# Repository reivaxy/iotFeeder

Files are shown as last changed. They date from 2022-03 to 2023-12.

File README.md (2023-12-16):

# iotFeeder

Page in french or other languages: https://github-com.translate.goog/reivaxy/iotFeeder?_x_tr_sl=en&_x_tr_tl=fr&_x_tr_hl=fr

## WiFi enabled fish feeder for aquarium. Notifies when empty, power off, ...

Main components: ESP8266, Oled screen, stepper motor, 3D printed Archimedes screw and case.

All settings are done using embedded web page forms over Wifi. It records activiyy in a Firebase DB (Google Cloud), and you will receive notifications when it's empty or offline.

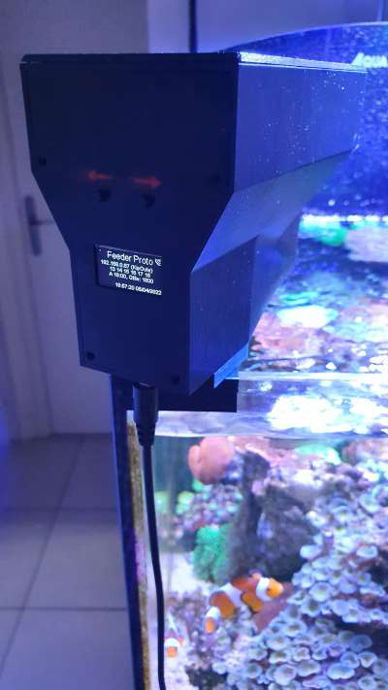
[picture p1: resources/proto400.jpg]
proto

```
DISCLAIMER of liability: this is a (fish) life sustaining device, all files are provided with no warranty of any kind. 

Building this device using these files and instructions means you implicitely accept to use it at your own risk, with proper supervision and monitoring to ensure your fishes are indeed fed as they should.

I can't be held responsible for any damage occurring while using a device you built using these files and instructions, whatever the reason (design flaw, software bug, ...)

If you do not agree with this disclaimer, do not build this device, or do not use it.
```

I've built 7 feeders with food IR detection (and one without), and a friend has built one.

4 are currently installed on small to big recifal fish tanks (salted water, tropical fishes and corals), and three on freshwater tank, running with no issue since begining of May 2022 for 2 of them, and since mid July 2022 for the others.

It will eventually be a module of the Iotinator framework (https://github.com/reivaxy/iotinator), but it can already work autonomously (no master module is needed).

It connects to your home Wifi network to fetch date/time and posts logs and alerts to Firebase (Google Cloud free account) as well as send push notifications when it detects that it's empty. Firebase will also send you push notifications when the module seems to be disconnected (power outage, wifi outage...)

It keeps working even if wifi goes out, but you'll get disconnection notifications, thanks to a google cloud function checking for ping records every 5mn.

Notifications are sent using Pushover.net, using a one-time-fee plan (about $5).

Logs and alerts are available on a google cloud application page:

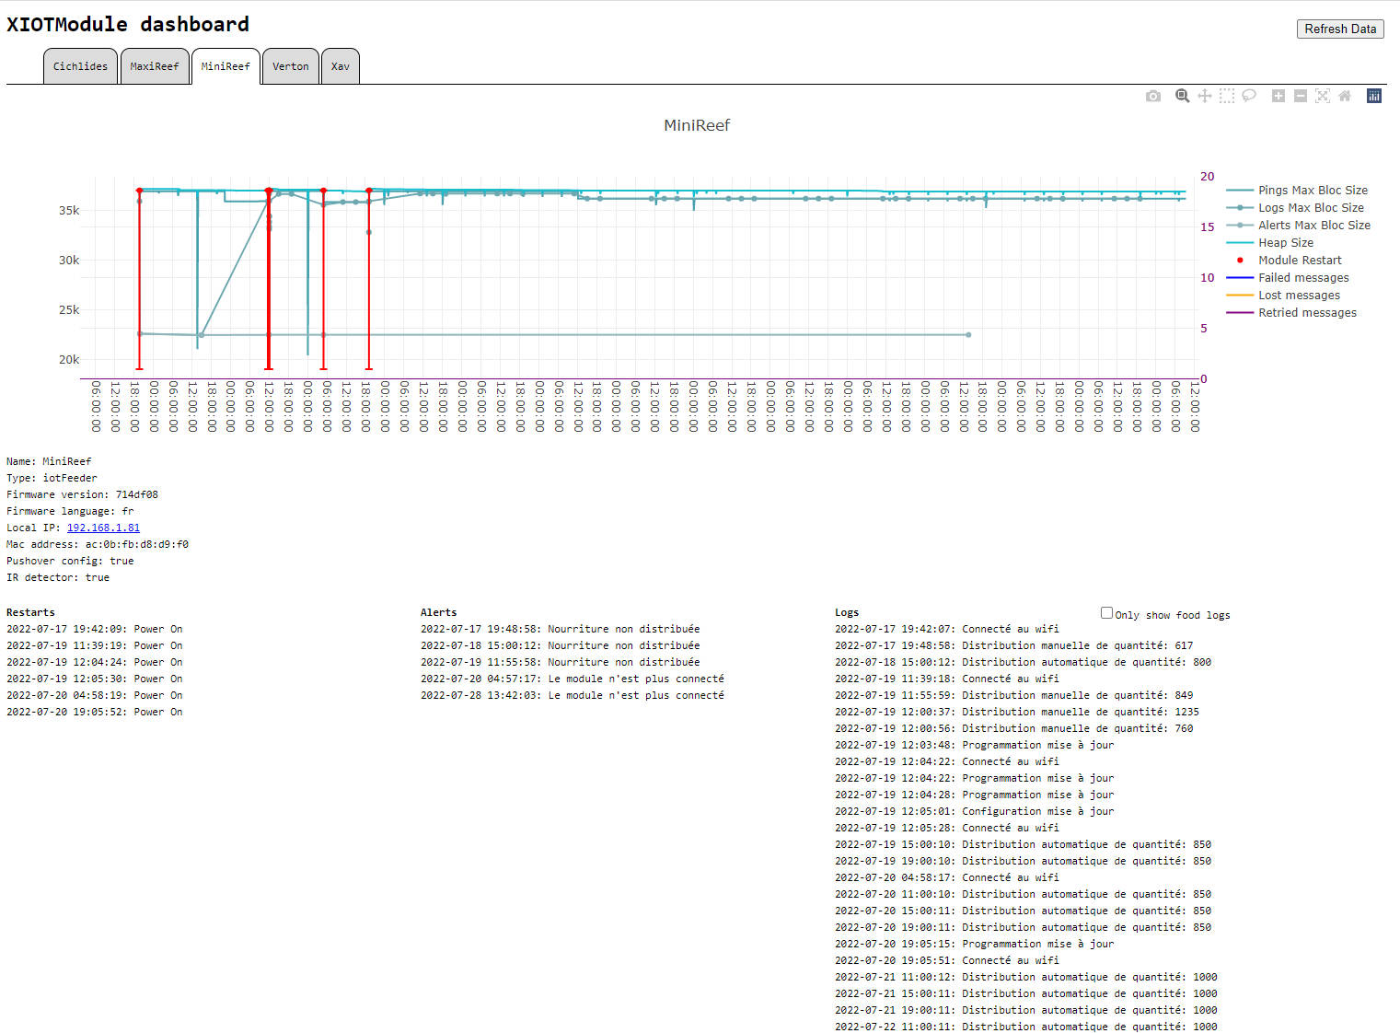
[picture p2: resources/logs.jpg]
logs


It's using cheap and widely available components (each under $4), a 3D printed case, and an optional but recommended PCB.

Firebase is used within the free offer allowances, so the overall cost should not exceed about $25.

The ESP8266 allows some WiFi access for setting the feeding times and quantities, as well as OTA firmware upgrade, the tiny Oled screen displays what's going on, and one push button helps calibrating the quantities as well as manually treat your little fishes when they deserve it.

The stepper motor allows controling with precision the amount of food dispensed.

Here is the overall aspect of the 3D printed case (before the addition of IR food dispensing detection)

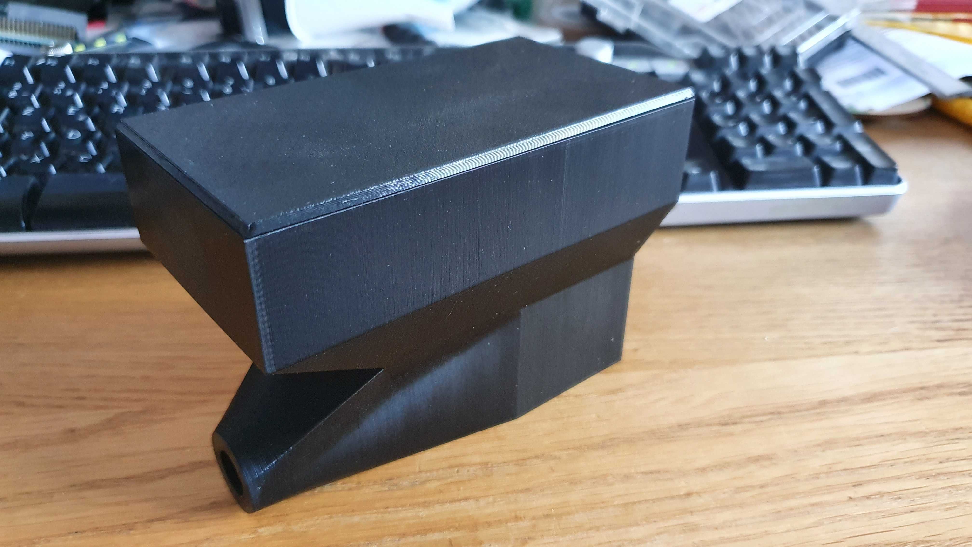
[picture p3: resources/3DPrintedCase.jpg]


Here is a working prototype:

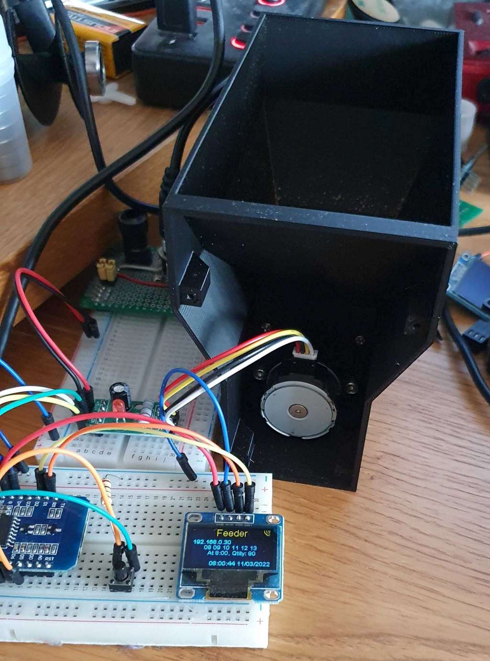
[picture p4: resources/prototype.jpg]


The 3D design is using an Archimedes' screw:

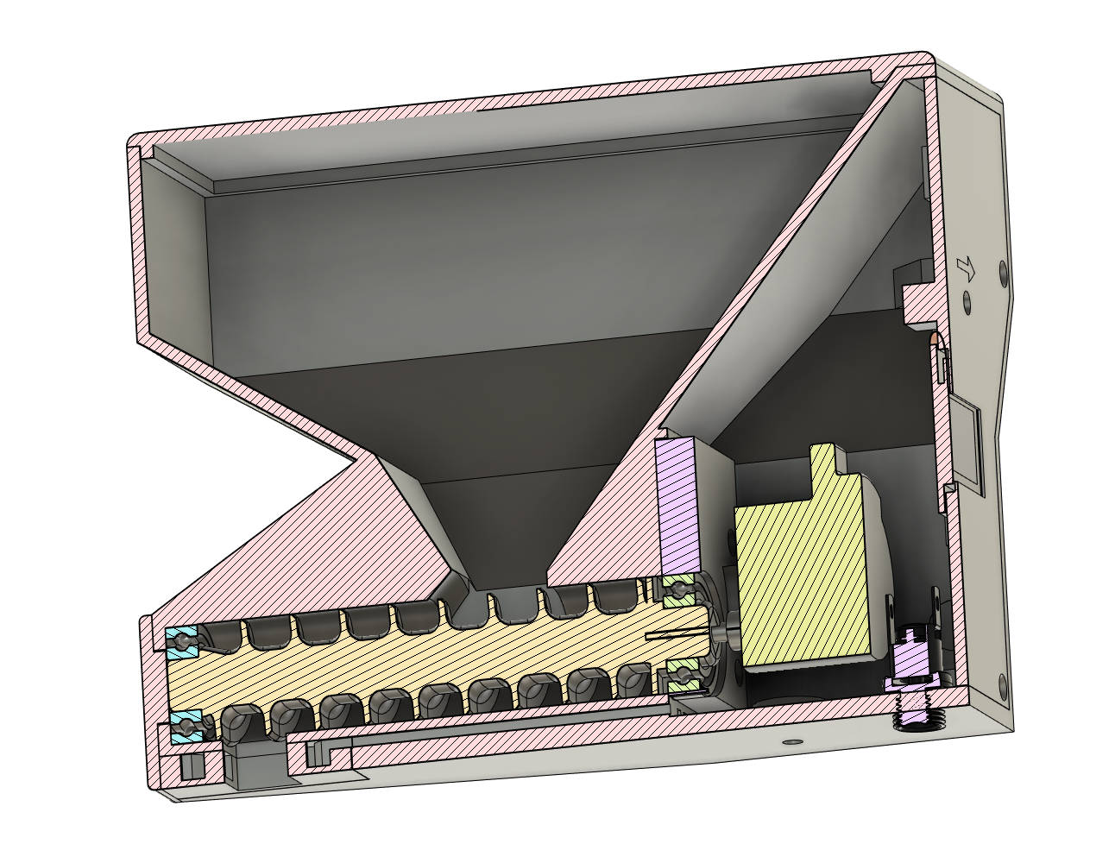
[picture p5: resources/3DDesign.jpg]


Here is a short demo with the prototype showing the configuration page, then the Oled screen, then the dispensing of one programmed serving.

https://youtu.be/9wqxyTTBjuU

## BUILDING YOURS

If you intend to build one, please first check the [wiki for assembling instructions](https://github.com/reivaxy/iotFeeder/wiki) with many pictures (work in progress).

And feel free to let me know, I might help with suggestions or latest info not already updated here.

I also offer to send you free of charge the two very tiny PCBs needed for the infrared sensors, since I have a few hundreds of them.

## COMPONENTS NEEDED

I've used this stepper driver board but I guess others should work:

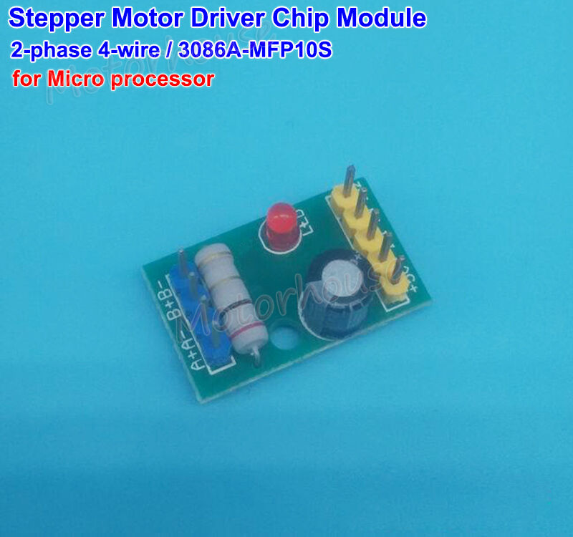
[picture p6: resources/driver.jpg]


https://www.ebay.com/itm/263017459366

To use them with the [PCB available here](hardware/PCB), you will need to unsolder the headers and solder them on the other side of the driver PCB, which is not ideal. 

This driver board was obviously not intended to be mounted on proto board but if you push hard enough, it fits :)

I might end up designing another PCB with an SMD MPF10S equivalent and the few discreete components needed to get rid of the driver board.

I've used this stepper, so the case is designed to accomodate it, but since it's mounted on an [independant plate](https://github.com/reivaxy/iotFeeder/blob/master/hardware/3DFiles/stepperPlate.stl), adaptation to another stepper could be easy if within the overall dimensions.

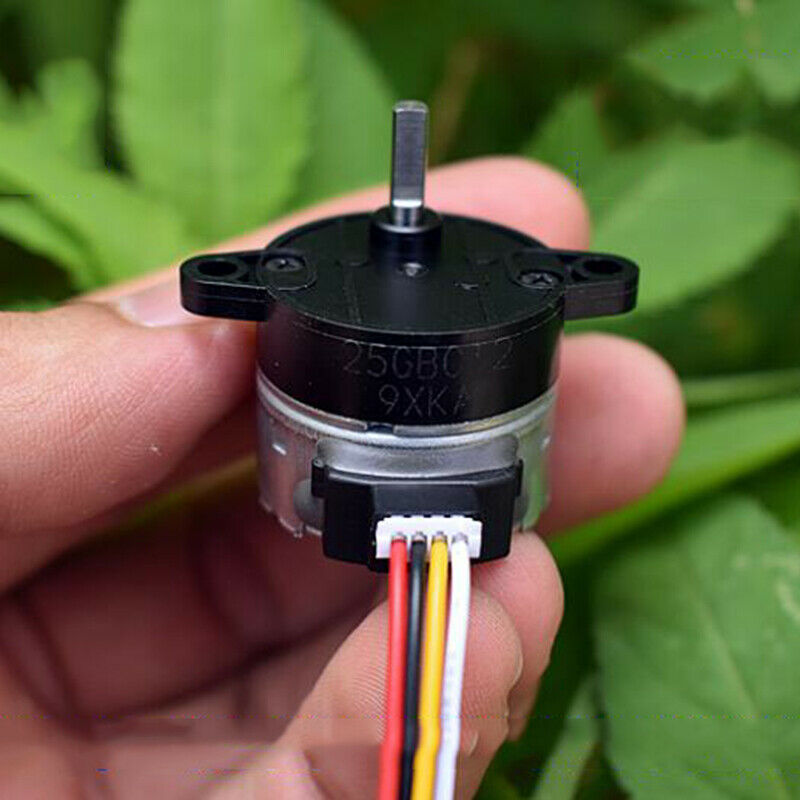
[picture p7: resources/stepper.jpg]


December 2023 edit: the ebay link I provided is no longer showing this stepper which may now be difficult to find :( 

Other components easy to find anywhere:

1 x ESP12 but it also works on a D1_mini or node MCU.

1 x LM1117 regulator (the stepper is 6V, the ESP 3.3V)

1 x Oled 0.96inch white pixels (the split blue & yellow screen does not age as well, and be careful with the power pins, some are reversed)

2 x push buttons (can be mounted on the [PCB](hardware/PCB) or wired)

5 x 10kΩ to 22kΩ resistors (SMD 0806 if you use the [PCB](hardware/PCB))

1 x 100Ω resistor (SMD 0806 if you use the [PCB](hardware/PCB))

1 x 51Ω resistor (SMD 0806 if you use the [PCB](hardware/PCB))

2 x 10µF capacitors (SMD 0806 if you use the [PCB](hardware/PCB))

1 x 6V power unit. The module needs about 500mA at peak when stepper starts, 100mA when idle 

1 x power jack socket

2 x 6800ZZ bearings

2 hex bolts m3x16 to mount the stepper on the stepper plate

8 Philips self tapping flat head screws m2x12 : 
- 4 to attach the stepper plate to the case
- 4 to attach the back panel to the case

 About 160g of PLA filament.

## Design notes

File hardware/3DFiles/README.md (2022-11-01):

# Fish feeder 3D files

The case was designed to be printable with no support, except for the "roof" of the IRInsert opening that may need some basic supports.

The archimedes's screw is printed in two halves that are joined by the bearing at each end. There is no need to glue the two halves together.

3 versions of the screw are available: 6 rotations, 9 rotations and 12 rotations.

If you need to dispense small quantities, higher rotation count will provide the best accuracy.

The stepper plate could be replaced by another one to accomodate a different stepper if within the overall dimensions, withouth a need to redesign the full case.

The holes to attach the stepper to the plate using hex bolts are printed "blind": this is a printing trick to have a decent result when printing overhung holes without supports. You just need to push the screw through the first time to break the thin layer, and may be clean up a little bit with a scalpel.

There are several options to fix the case to the aquarium in the "foot" directory, they all offer the case rotation on the vertical axis (thanks to a printed big screw whose two halves need to be printed horizontally), one offers translating back and forward. This needs more documenting coming soon.

The back comes in two flavors, a plain one that you print as usual, and a bi-color one that features arrows on top of the push button holes, that you can print with a printer handling several colors (2 heads, Prusa MMU, or Palette)

The tray for Infra Red sensors comes in two flavors too, check the IRTray directory README.

If you need a bigger food tank two extensions that clip on top of the case are available (20 or 45mm) and can easily be customized to fit whatever need.

Check the wiki for details on printing each part.

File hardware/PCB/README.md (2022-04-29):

Here are the gerber file to order PCBs

I left the text file with the coordinates of JLCPCB, a Chinese firm who does a very good job, quickly and for a low price.

For this board, I've ordered 10 pieces for about $10 shipping included.

WARNING: on PCB v1, I was using GPIO9, which should not be used => had to cut a track and add a wire. Also, no decoupling capacitor on the regulator, but it worked fine.

PCB v2 fixes all this, and provides support for infra red sensor.

Top layer:

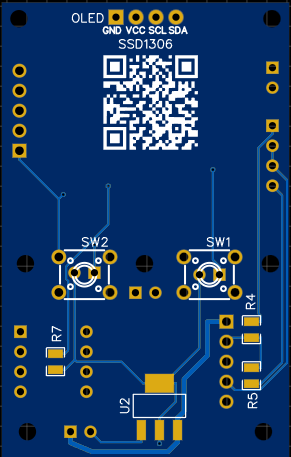
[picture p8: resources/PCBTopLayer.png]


Bottom layer:

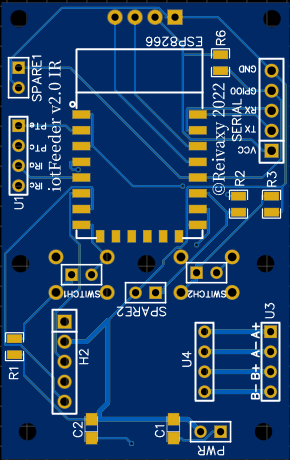
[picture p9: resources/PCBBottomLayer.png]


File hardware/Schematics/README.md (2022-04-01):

Here is the schema. I designed it using the https://easyeda.com/ schema editor which is online, free, and brilliant.

It also allows to design the PCB and order it in a few clicks.

On PCB v1 I forgot to add capacitors around the LM1117 :( PCB v2 will have them.

In theory, SCL/SDA pins should have pullup resistors, but I never used any when driving one of these OLED screens, and all worked fine, at least as long as you do not use this bus to control several devices.

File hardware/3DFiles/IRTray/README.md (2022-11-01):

# Infrared sensor tray

This is a new version of the original IRTray.stl file designed to better protect the sensors against water splashes and food crumbs.

Depending on your printer capabilities, you can either :

- print just the IRTrayFullTranslucent.stl file using translucent filament

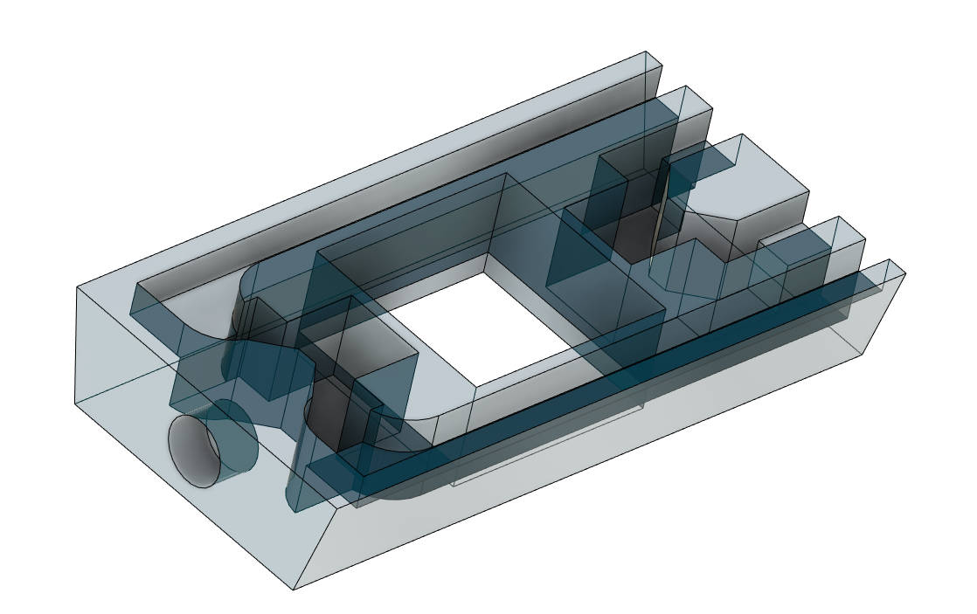
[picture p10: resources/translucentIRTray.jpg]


- or if you printer can print with several materials (like Prusa with MMU2) use both IRTrayInsertTranslucent.stl AND IRTrayShell.stl in one print, and use translucent filament for the former part and whatever color you print the feeder case for the latter.

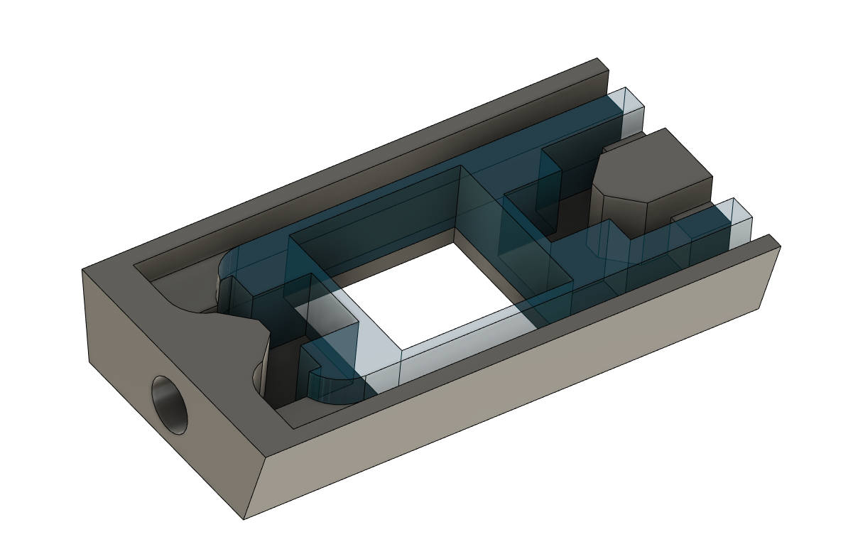
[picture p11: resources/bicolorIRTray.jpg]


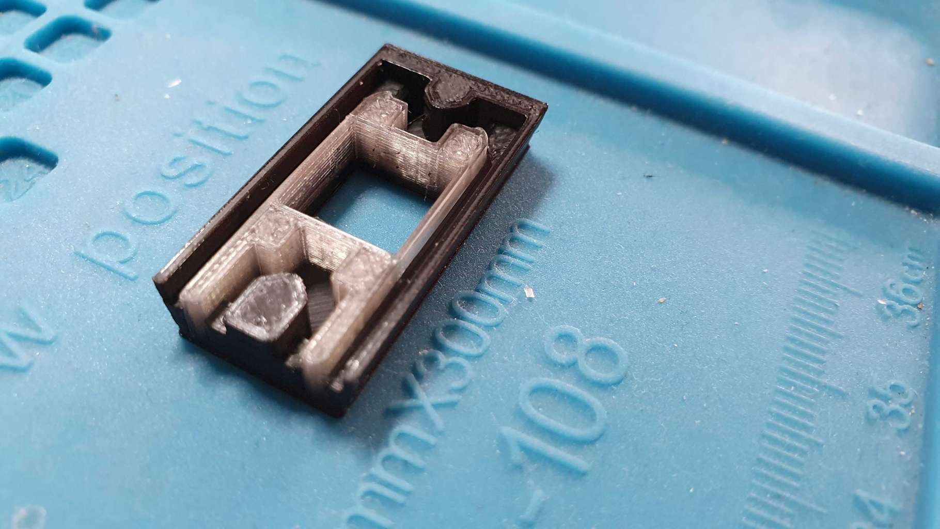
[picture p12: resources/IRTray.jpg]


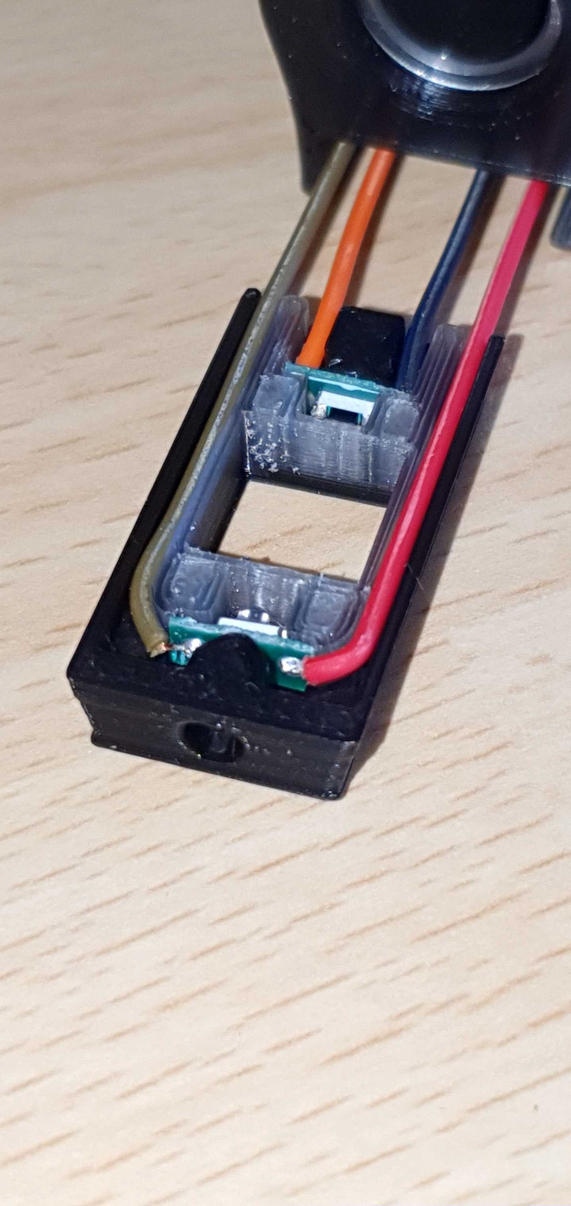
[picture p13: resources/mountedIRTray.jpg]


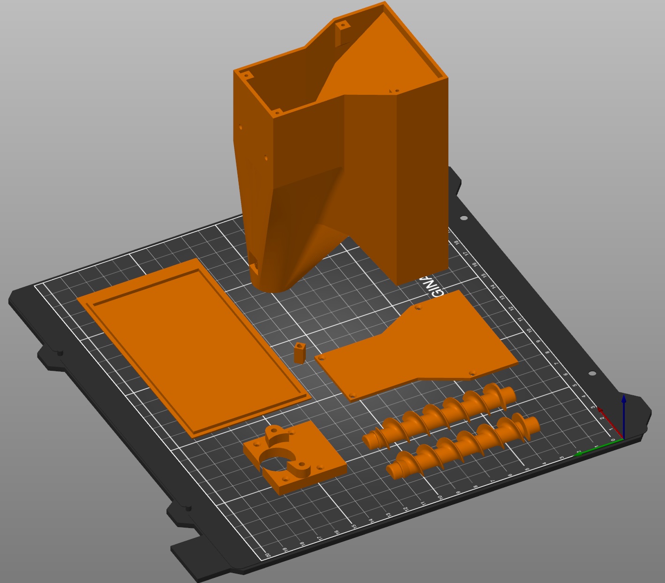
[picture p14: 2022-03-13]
resources/3Dprinting.jpg

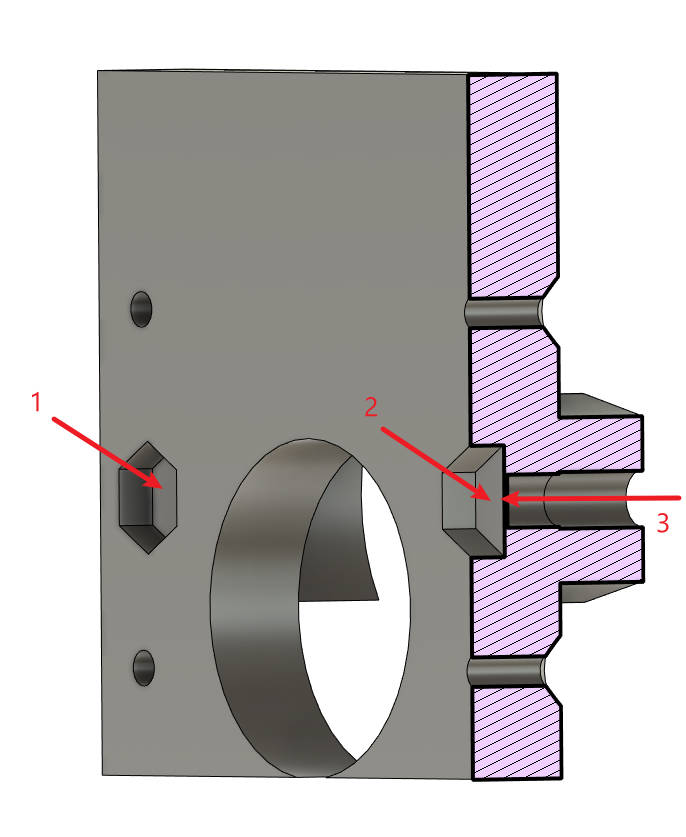
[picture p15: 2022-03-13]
resources/boltBlindHoles.jpg

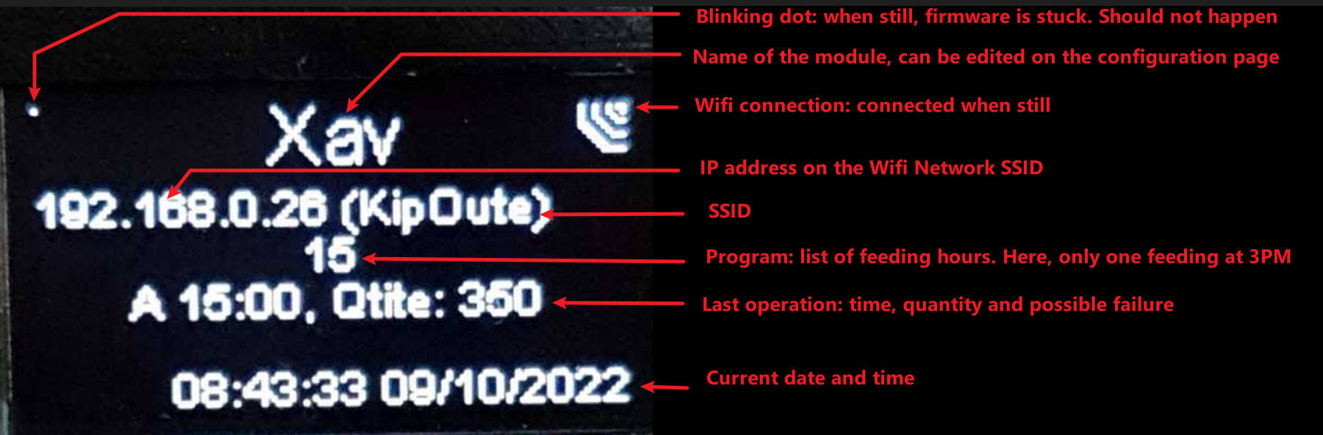
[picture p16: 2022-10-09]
resources/display.jpg

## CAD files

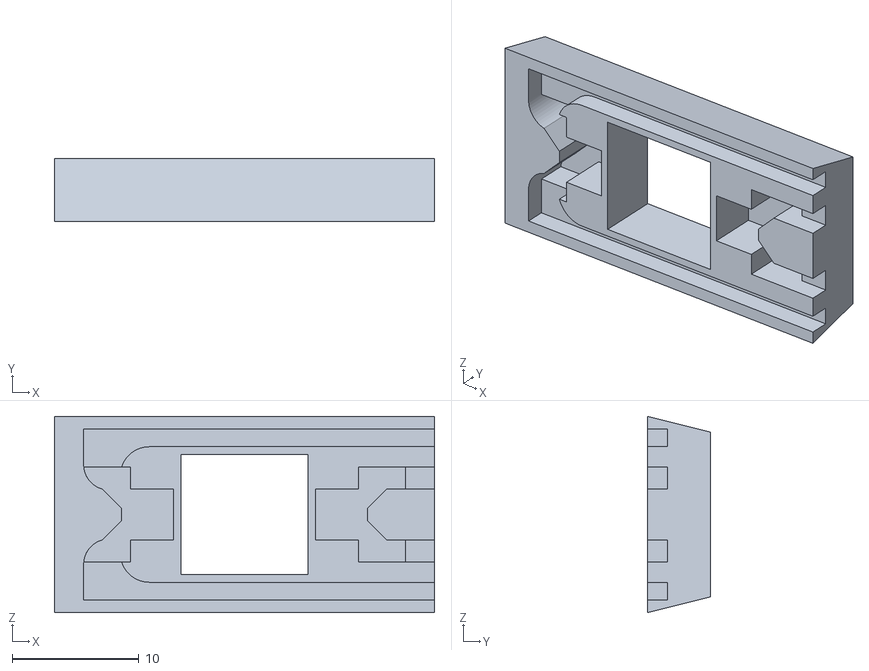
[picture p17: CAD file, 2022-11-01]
hardware/3DFiles/IRTray/IRTrayFullTranslucent.stl
30.0 x 5.00 x 15.5

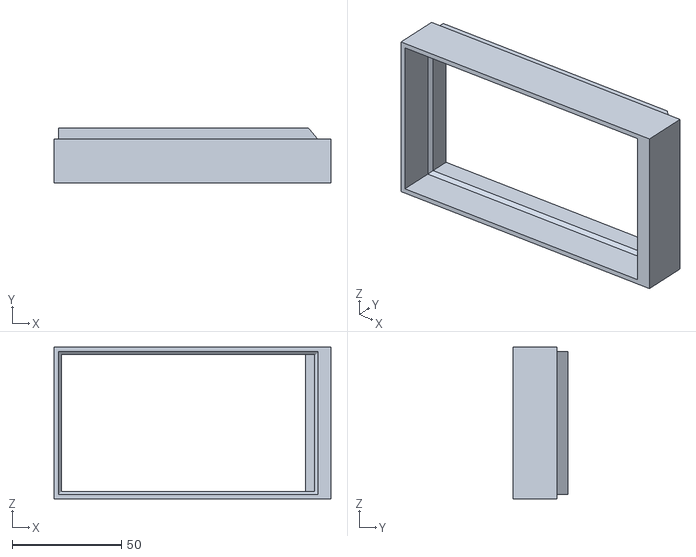
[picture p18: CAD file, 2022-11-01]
hardware/3DFiles/extension20.stl
127.0 x 25.0 x 69.6

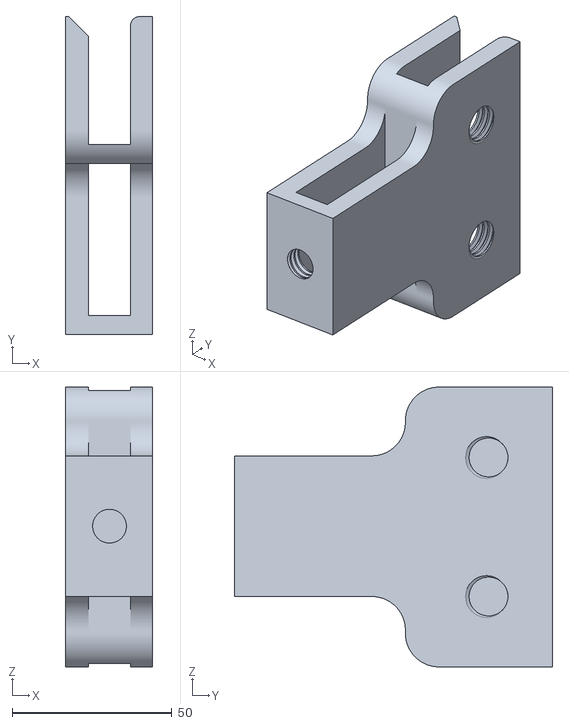
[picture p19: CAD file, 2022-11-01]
hardware/3DFiles/foot/highClamp.stl
27.3 x 99.4 x 87.5

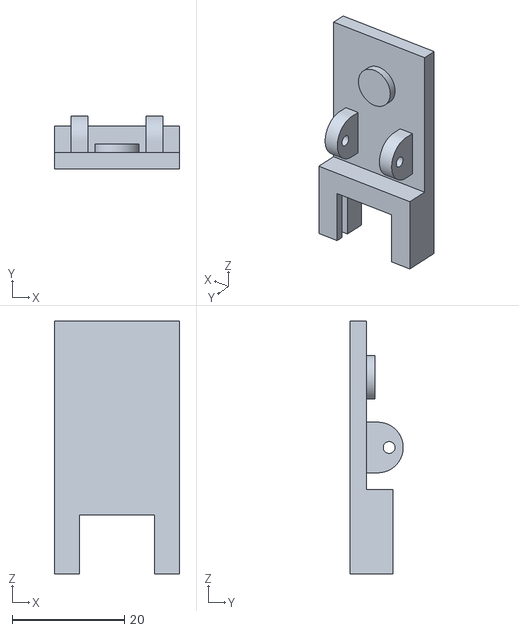
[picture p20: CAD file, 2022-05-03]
hardware/3DFiles/serialConnectionClamp/serialClampTop.stl
22.3 x 9.50 x 45.0

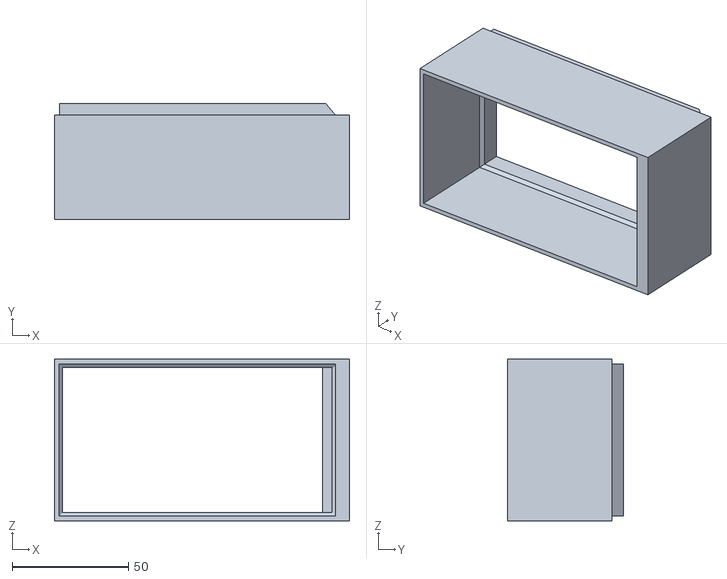
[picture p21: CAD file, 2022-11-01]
hardware/3DFiles/extension45.stl
127.0 x 50.0 x 69.6

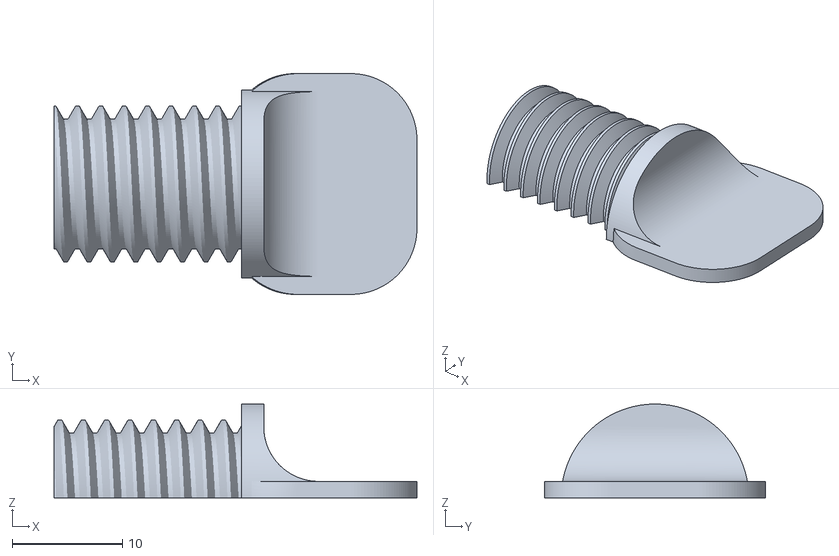
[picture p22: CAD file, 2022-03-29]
hardware/3DFiles/foot/tightener_1.stl
32.9 x 20.0 x 8.50

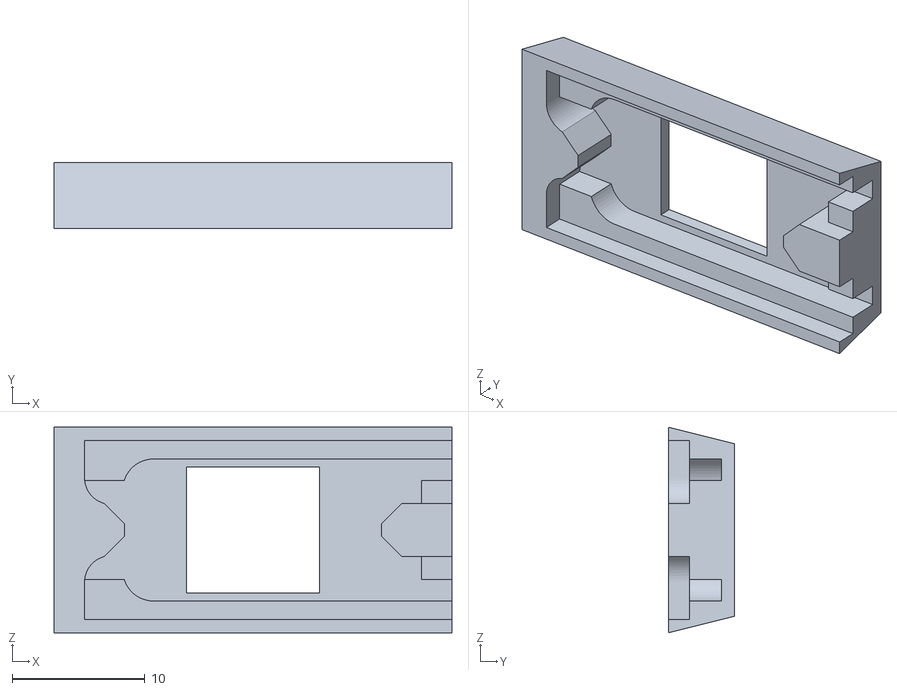
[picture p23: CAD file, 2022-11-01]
hardware/3DFiles/IRTray/IRTrayShell.stl
30.0 x 5.00 x 15.5

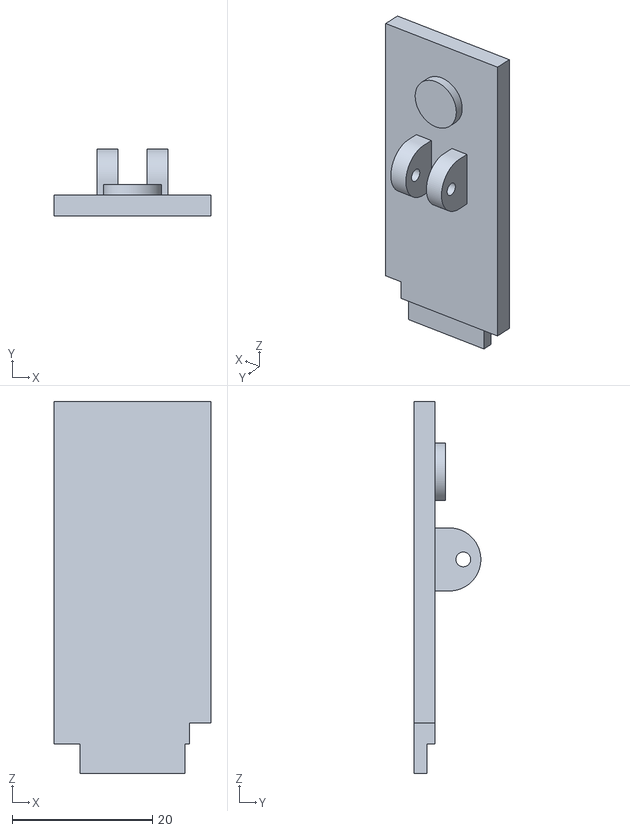
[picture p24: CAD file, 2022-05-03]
hardware/3DFiles/serialConnectionClamp/serialClampBottom.stl
22.3 x 9.50 x 53.0

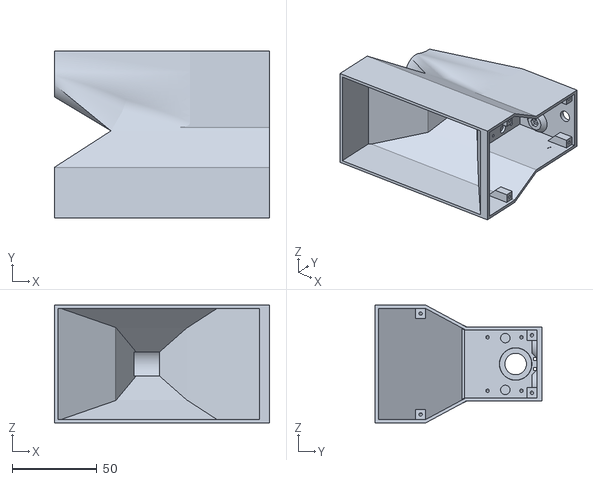
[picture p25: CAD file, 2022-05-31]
hardware/3DFiles/caseBottomPowerJack.stl
127.0 x 98.7 x 69.6

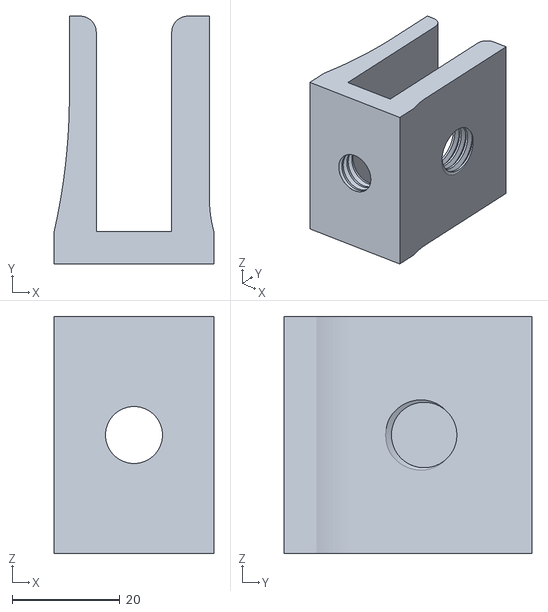
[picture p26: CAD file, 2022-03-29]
hardware/3DFiles/foot/bigClamp.stl
29.7 x 46.0 x 44.0

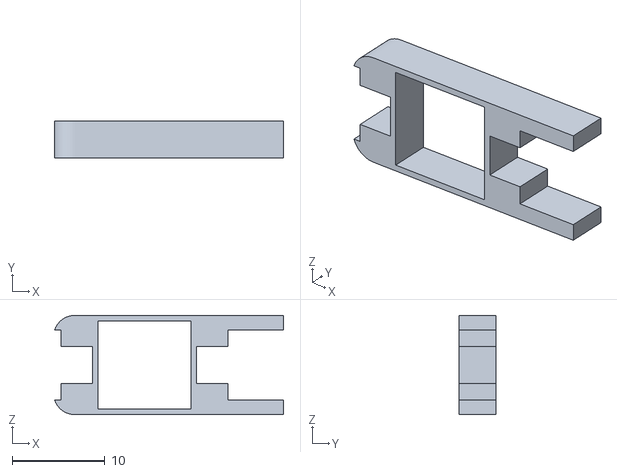
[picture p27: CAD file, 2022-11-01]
hardware/3DFiles/IRTray/IRTrayInsertTranslucent.stl
24.7 x 4.00 x 10.7

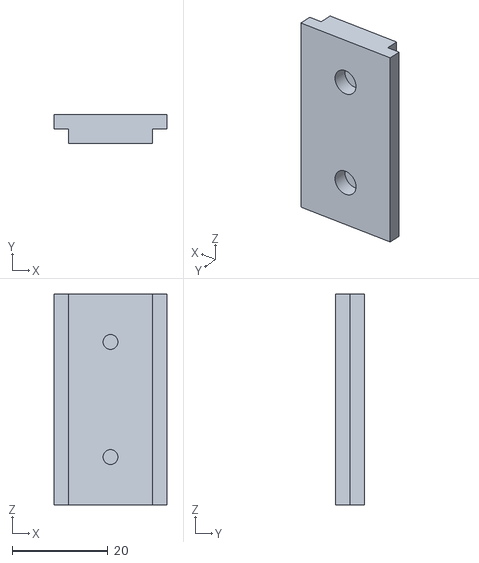
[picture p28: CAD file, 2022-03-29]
hardware/3DFiles/foot/railBase.stl
23.5 x 6.00 x 44.0

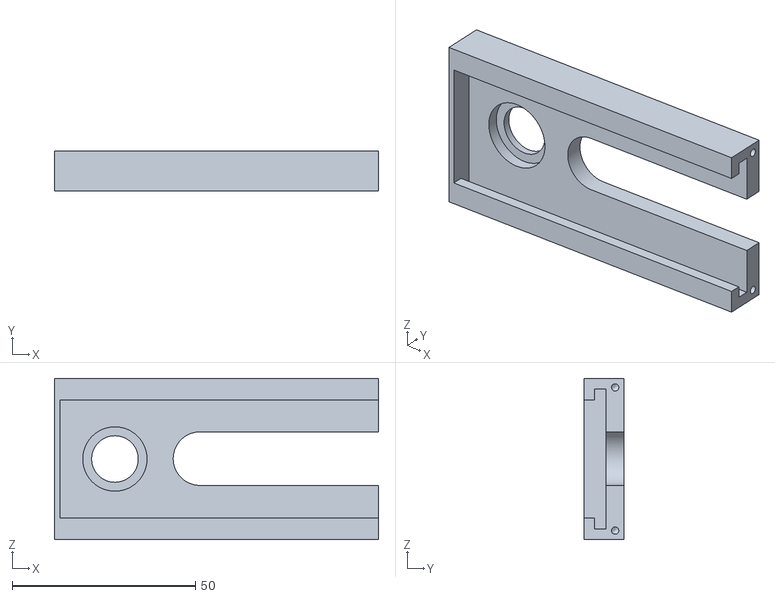
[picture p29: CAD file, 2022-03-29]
hardware/3DFiles/foot/parallelRail.stl
88.5 x 11.0 x 44.0

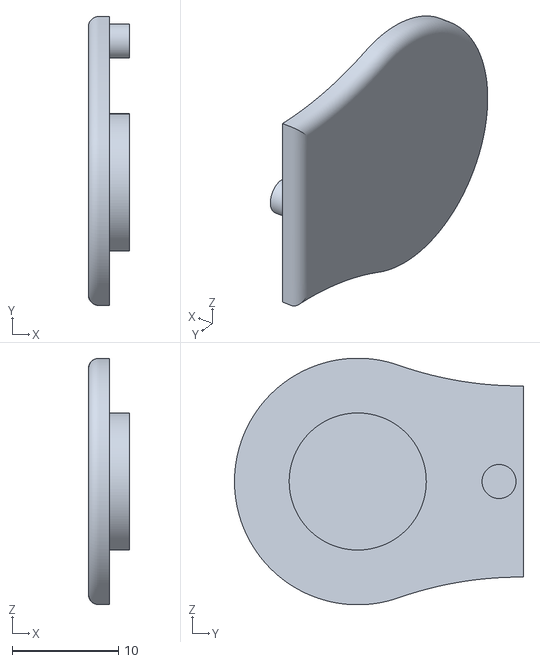
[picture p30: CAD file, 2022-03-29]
hardware/3DFiles/bearingCover.stl
3.90 x 27.2 x 23.2

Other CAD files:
hardware/3DFiles/caseLeftSidePowerJack.stl
hardware/3DFiles/caseRightSidePowerJack.stl
hardware/3DFiles/foot/rail.stl
hardware/3DFiles/foot/tightener.stl
hardware/3DFiles/backNoArrows.stl
hardware/3DFiles/backWithArrows.stl
hardware/3DFiles/foot/backStopper.stl
hardware/3DFiles/foot/base.stl
hardware/3DFiles/foot/clamp.stl
hardware/3DFiles/foot/parallelRailBase.stl
hardware/3DFiles/foot/pivot.stl
hardware/3DFiles/foot/pivot_1.stl
hardware/3DFiles/foot/smallClamp.stl
hardware/3DFiles/forwardArrow.stl
hardware/3DFiles/insert.stl
hardware/3DFiles/reverseArrow.stl
hardware/3DFiles/screw12-1.stl
hardware/3DFiles/screw12.stl
hardware/3DFiles/screw6-1.stl
hardware/3DFiles/screw6.stl
hardware/3DFiles/screw9-1.stl
hardware/3DFiles/screw9.stl
hardware/3DFiles/stepperPlate.stl
hardware/3DFiles/top.stl

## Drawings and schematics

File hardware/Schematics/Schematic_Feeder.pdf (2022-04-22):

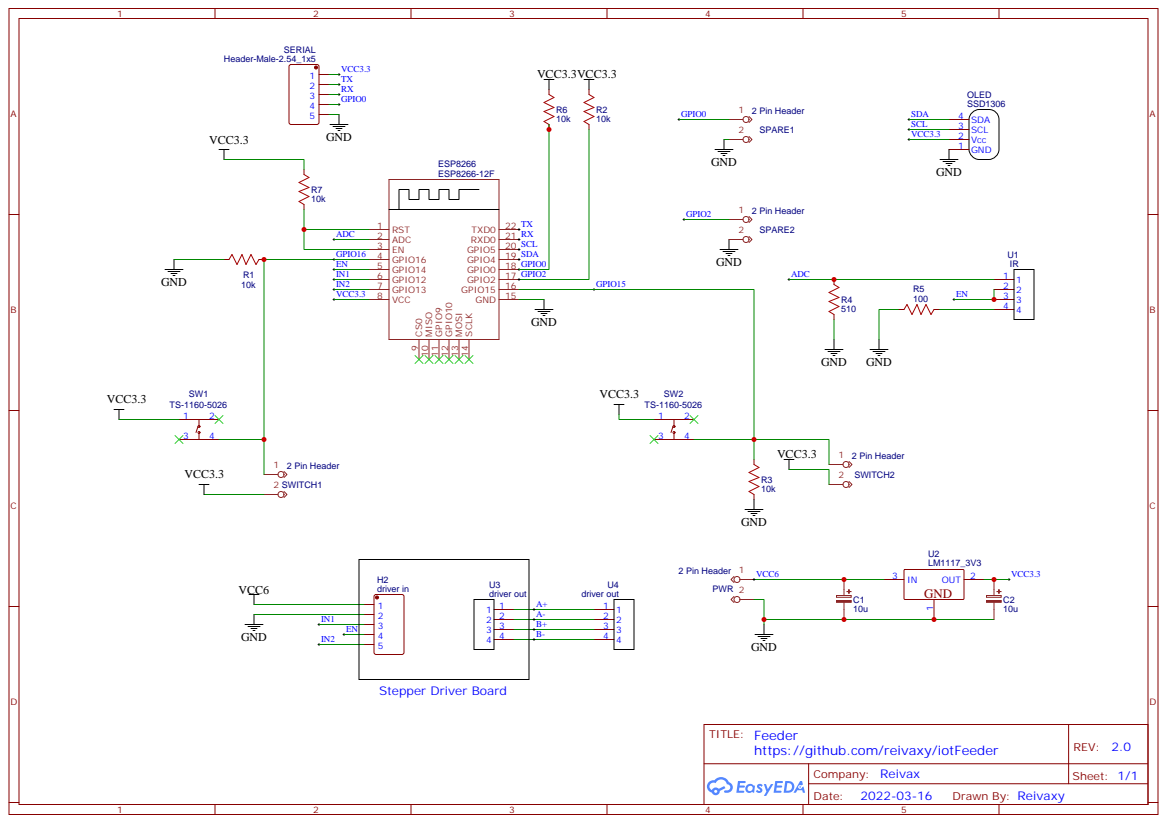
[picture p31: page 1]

TITLE: Feeder
https://github.com/reivaxy/iotFeeder

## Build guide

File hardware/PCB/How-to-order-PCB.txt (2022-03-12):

How to Order PCB

Please refer to:
https://docs.easyeda.com/en/PCB/Order-PCB

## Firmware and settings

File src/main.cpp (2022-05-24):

/**
 *  iotinator Feeder module
 *  Xavier Grosjean 2022
 *  Creative Commons Attribution-NonCommercial-ShareAlike 4.0 International Public License
 */
 
#include <stdio.h>
#include "FeederModule.h"
#include "config.h"

#define API_VERSION "1.0"    // modules can check master API version to make sure they are compatible...(still unused)

// Global object to store config
FeederConfigClass *config;
XIOTModule* module;

int scl = 5; 
int sda = 4; 
// Remember, never use gpio 9 and 10 on esp12e :(
int reversePin = 16;  
int forwardPin = 15;

void setup() {
  char stackStart;
  Serial.begin(115200);
  config = new FeederConfigClass((unsigned int)CONFIG_VERSION, (char*)MODULE_NAME);
  config->init();
  // to avoid side effects when these pins are not connected. Huh, too late, useless I think
  pinMode(0, OUTPUT); digitalWrite(0, HIGH);
  pinMode(2, OUTPUT); digitalWrite(2, HIGH);
  module = new FeederModule(config, 0x3C, sda, scl, forwardPin, reversePin);
  module->setStackStart(&stackStart);
}

void loop() {
  // Mandatory periodic call, to refresh display, Clock, check requests
  // on the http API, ...
  module->loop();
}

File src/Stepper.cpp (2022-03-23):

/**
 *  iotinator iotFeeder Agent module
 *  Xavier Grosjean 2022
 *  Creative Commons Attribution-NonCommercial-ShareAlike 4.0 International Public License
 */


#include "Stepper.h"

Stepper::Stepper() {
   stepper = AccelStepper(AccelStepper::FULL2WIRE, IN1, IN2);
   stepper.setEnablePin(EN);
   stepper.setCurrentPosition(0);
   stepper.setMaxSpeed(200.0);
   stepper.setAcceleration(100.0);
   stepper.disableOutputs();
   stepCount = 0;
}

void Stepper::start(long count) {
   firstStep = true;
   stepper.move(count);
   stepper.enableOutputs();
}

long Stepper::remaining() {
   return stepper.distanceToGo();
}

void Stepper::run() {
   firstStep = false;
   stepper.run();
}

boolean Stepper::isFirstStep() {
   return firstStep;
}

void Stepper::stop() {
   stepper.stop();
   stepper.setCurrentPosition(0);
   stepper.disableOutputs();
}

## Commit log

2022-03-06 Feeder with an sarchimedes screw
    [back.stl, case.stl, insert.stl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]
2022-03-10 Ascii STLs
    [back.stl, case.stl, insert.stl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]
2022-03-10 Added Stepper, now working according to time schedule
2022-03-11 Added push button to calibrate quantities
2022-03-12 Adding schematics and PCB
    [Drill_NPTH_Through.DRL, Drill_PTH_Through.DRL, Gerber_BoardOutlineLayer.GKO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]
2022-03-12 Hanlding 2nd switch for reverse movement
    [FeederModule.cpp, Stepper.cpp, main.cpp]
2022-03-13 added prototype video
2022-03-13 various adjustements
    [back.stl]
2022-03-20 Adding 3D files for clamp
    [backWithArrows.stl, base.stl, base2.stl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]
2022-03-23 IR detection only when Stepper Enabled Detects no food through IR and output message
2022-03-23 Moving backward no longer triggering no food alert
    [FeederModule.cpp]
2022-03-29 New case with IR support
    [IRinsert.stl, backNoArrows.stl, backStopper.stl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]
2022-03-29 Lowered memory footprint using PROGMEM Added differed log sending
2022-04-01 Updating schematics to v2
2022-04-02 directive to handle pcbv1
2022-04-03 Fixed gpio9 and firebase messages
    [FeederModule.cpp, main.cpp]
2022-04-10 can revert from web page
    [FeederModule.cpp]
2022-04-22 gpio 9 & 10 must not be used
    [Drill_NPTH_Through.DRL, Drill_PTH_Through.DRL, Gerber_BoardOutlineLayer.GKO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]
2022-04-25 Fixed screen brightness init from config
    [FeederModule.cpp]
2022-04-29 Added case variants with power jack on either side
    [backStopper.stl, base.stl, bigClamp.stl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]
2022-05-03 easier mounting IRInsert file
    [IRinsert.stl, serialClampBottom.stl, serialClampTop.stl]
2022-05-09 Manual feeding messages no longer transient Fixed missing translations
    [FeederModule.cpp]
2022-05-31 Fixed case powerjack pre-holes
    [case.stl, caseBottomPowerJack.stl, caseLeftSidePowerJack.stl]
2022-11-01 New IR tray and high clamp
    [IRTrayFullTranslucent.stl, IRTrayInsertTranslucent.stl, IRTrayShell.stl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]
2022-11-01 Food tank extensions
    [extension20.stl, extension45.stl]
2023-12-16 removed dead link to stepper motor
